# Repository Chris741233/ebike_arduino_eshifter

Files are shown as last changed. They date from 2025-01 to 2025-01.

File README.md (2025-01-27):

# ebike_arduino_eshifter
 eshifter for reconditioned VanMoof s5 ebike

Aide au membre de Cyclurba Kiki85 pour son reconditionnement d'un ebike VanMoof s5  
Aduino Nano/Uno, signal +5V, alim 9V.

**Discussion sur le forum Cyclurba**  - [Cyclurba](https://cyclurba.fr/forum/757849/programme-arduino-schifter.html?discussionID=31918)  
Site VanMoof - [VanMoof](https://www.vanmoof.com/fr-FR/our-rides/s5)

Librairies à installer, voir dossier "library_zip"  
Code de calibrage moteur et intensité, voir "arduino_eshifter_calibrage"  
Code d'utilisation voir "arduino_eshifter"  

---
#### VanMoof s5 eshifter
<p align="left">
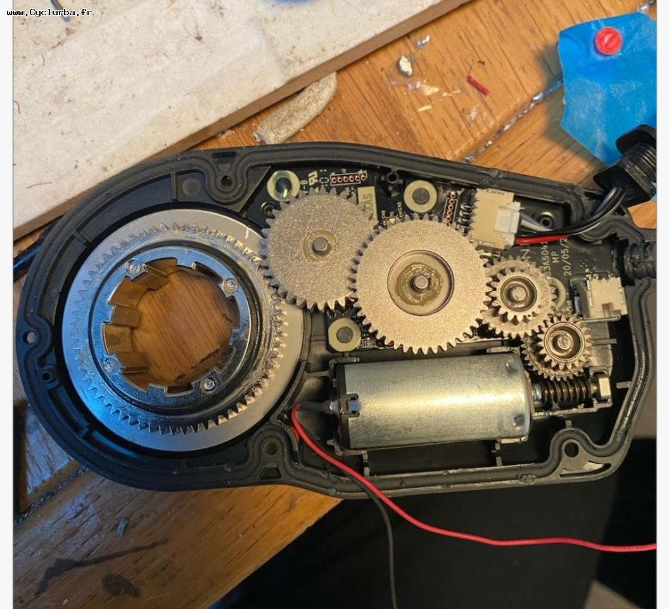
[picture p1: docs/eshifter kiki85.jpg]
  
</p>

#### Banc test : Arduino Uno/Nano + L298N + INA219
<p align="left">
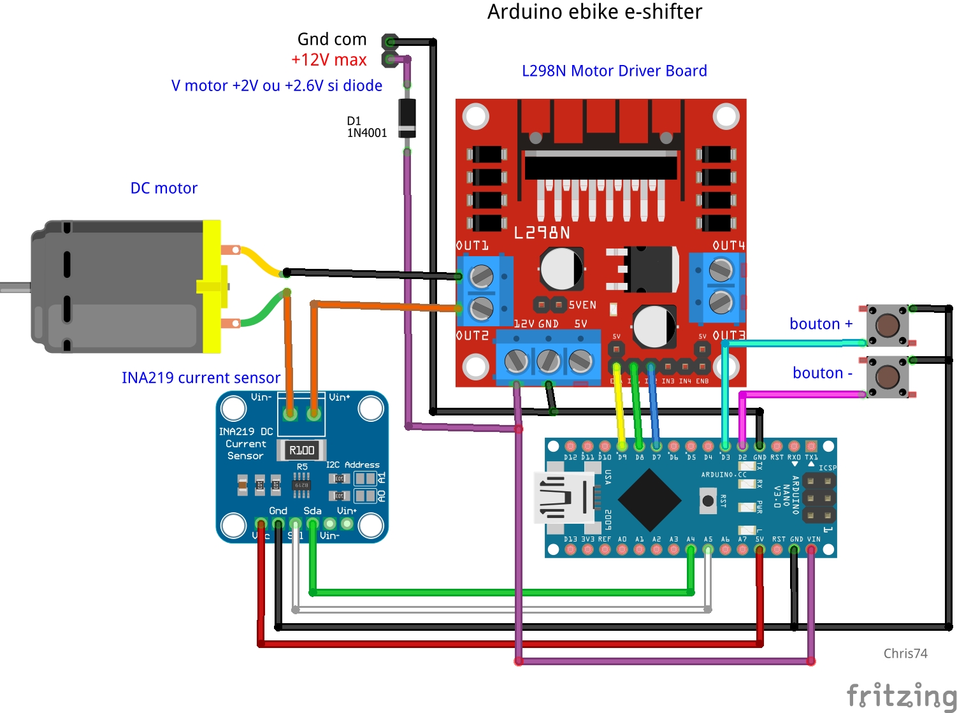
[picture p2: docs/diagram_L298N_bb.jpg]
  
</p>

#### Cavaliers circuit L298N
<p align="left">
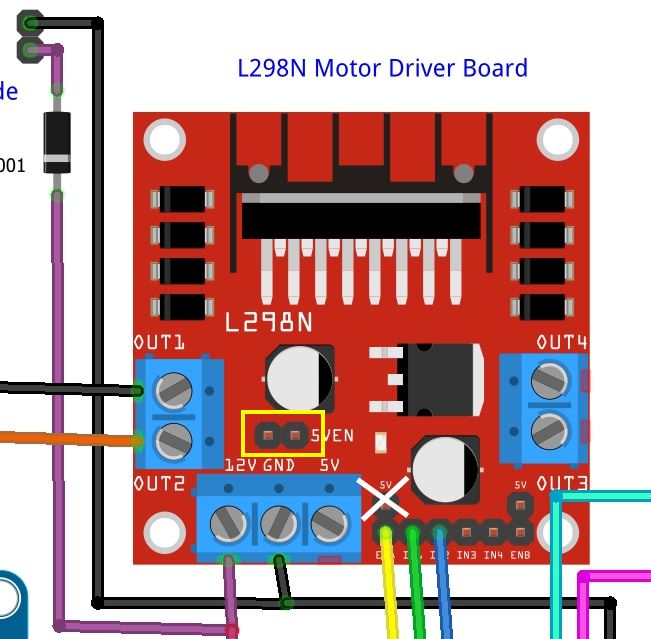
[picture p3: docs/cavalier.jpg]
  
</p>

#### Banc test
<p align="left">
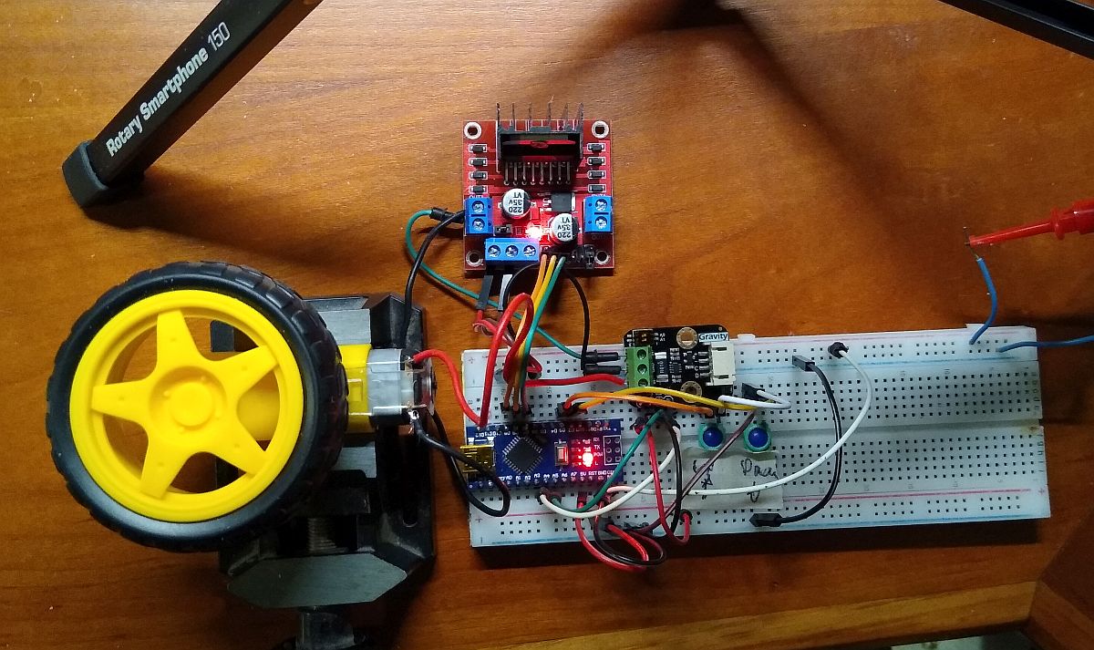
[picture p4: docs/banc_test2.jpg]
  
</p>

#### Console Serial (code de calibrage)
<p align="left">
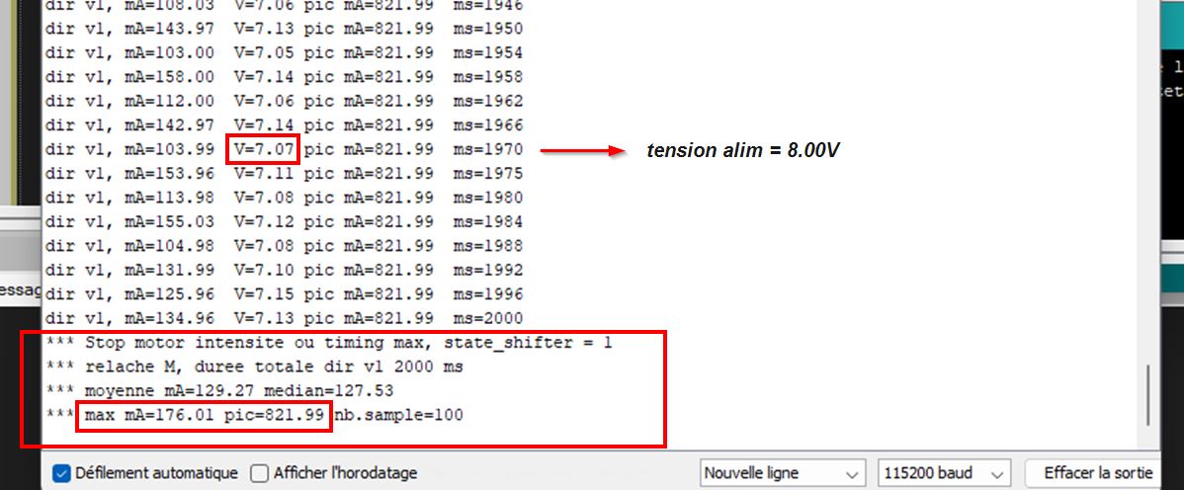
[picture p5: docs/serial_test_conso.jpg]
  
</p>
---

#### Utilisation
Régler les constantes en début de code selon vos essais, voir aussi le sujet sur le forum Cyclurba \
*Adjust constants at the beginning of code*

```
-- Setting ---

#define ADRESSE_INA 0x40     // adresse I2C INA219, generalement 0x40 (DFRobot=0x45) 
#define RSHUNT_INA 0.100     // valeur shunt, generalement R100 = 0.100 Ohm  (DFRobot=0.010) 
const int SPEED_MOTOR = 255; // speed moteur par defaut, 0 to 255 max (PWM 8bit)
const int MA_RUN = 360;      // (300) mA, conso en utilisation (sous ~6.5V au moteur)
const int MA_MARGE = 200;    // (150) mA, + marge de butee a pas depasser pour securite (stale = ? mA sous 8V)
const int MA_MAX = MA_RUN + MA_MARGE; 

// -- ces parametres influencent sur le controle intensite max moteur
const int SUP_PIC = 30;   // ms, filtrer les premieres ms du pic demarage moteur, env. 30-50=Ok ou 0 pour desactive
const int MIN_STAT = 20;  // mA, 20mA minimum pour etre affiche en direct et ajoute aux stats (laisser comme ca !)

const int TIMEOUT_1to3 = 2400;  // ms, temps de reference pour passer de v1 à v3 (butee basse a haute)
const int MARGE_HOME = 100;     // ms, petite marge a ajouter a TIMEOUT_1to3 pour etre sur de la position home v1 au boot
const int TIMEOUT_STEP = TIMEOUT_1to3/2; // ms, etape (1to2, 2to3, etc..), en principe TIMEOUT_1to3 / 2

const int DELAY_PUSH_BTN = 800; // ms, lorsqu'appui sur bouton et position atteinte (stop) = le delais d'attente avant reprise
// empeche relance moteur indesirable

const bool DOUBLE_CLIC_REINIT = true;  // reinit position home sur v1 si double-clic bouton down (descendre), true ou false

---
```

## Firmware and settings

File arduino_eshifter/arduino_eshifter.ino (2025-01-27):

/******************************************************************
Created with PROGRAMINO IDE for Arduino - 26.01.2025 | 13:38:17
Update      :
Author      : Chris74 pour Kiki85 (Cyclurba)
Description : e-shifter ebike Vanmoof s5, Arduino Nano

Github (codes et doc) : https://github.com/Chris741233/ebike_arduino_eshifter

forum Cyclurba : https://cyclurba.fr/forum/757849/programme-arduino-schifter.html?discussionID=31918


INA219 :
https://how2electronics.com/how-to-use-ina219-dc-current-sensor-module-with-arduino/
https://wiki.dfrobot.com/Gravity:%20I2C%20Digital%20Wattmeter%20SKU:%20SEN0291

L298N:
https://www.robotique.tech/tutoriel/commander-un-moteur-par-arduino-et-le-module-l298n/

conso montage a vide (Arduino nano + l298n + ina219) sous 8V = 29mA (sans USB, sans diode alim)

Voir aussi schema et script de calibration moteur et intensite

******************************************************************/


// -------- INCLUDE -------------------------------


#include <Wire.h>          // I2C
#include "INA219.h"        // from Rob.Tillaart, voir https://github.com/RobTillaart/INA219

// simplification envois Serial et screen serial, expl: Serial << "A:" << var << endl;
#include <Streaming.h>     // Peter Polidoro, https://github.com/janelia-arduino/Streaming    

// duree d'appui bouton et gestion bouton
// librairie du membre bricoleau, voir https://forum.arduino.cc/t/partage-boutons-poussoirs/361656
// pour info n'est pas dispo dans le depot officiel Arduino
#include "simpleBouton.h"  


#include <Timeout.h>       // timer, tfeldmann  https://github.com/tfeldmann/Arduino-Timeout 
// ne pas confondre avec TimeOut.h !


// -------- ARDUINO PIN, selon schema joint --------------

// butons
const int BUTON_UP_PIN = 3;    // bouton poussoir Plus (UP, Monter vers v3), interupt 3 possible  
const int BUTON_DOWN_PIN = 2;  // bouton poussoir Moins (DOWN, Descendre vers v1), interupt 2 possible

// L298N, motor driver
const int ENA_PIN = 9;   // enable A, PWM
const int IN1_PIN = 8;   // in1
const int IN2_PIN = 7;   // in2 

// LED interne Uno/Nano
const int LED_PIN = 13;  // LED_BUILTIN


// INA219 curent sensor  
// I2C PIN SDA A4, SCL A5


// --------  CONSTANTES SYSTEME, MODIFIABLES ------------------------


#define ADRESSE_INA 0x40     // adresse I2C INA219, generalement 0x40 (DFRobot=0x45) 
#define RSHUNT_INA 0.100     // valeur shunt, generalement R100 = 0.100 Ohm  (DFRobot=0.010) 

const int SPEED_MOTOR = 255; // speed moteur par defaut, 0 to 255 max (PWM 8bit)

const int MA_RUN = 360;      // (300) mA, conso en utilisation (sous ~6.5V au moteur)
const int MA_MARGE = 200;    // (150) mA, + marge de butee a pas depasser pour securite (stale = ? mA sous 8V)
const int MA_MAX = MA_RUN + MA_MARGE; 

// -- ces parametres influencent sur le controle intensite max moteur
const int SUP_PIC = 30;   // ms, filtrer les premieres ms du pic demarage moteur, env. 30-50ms=Ok ou 0 pour desactive
const int MIN_STAT = 20;  // mA, 20mA minimum pour etre affiche en direct et ajoute aux stats (laisser comme ca !)

const int TIMEOUT_1to3 = 2400;  // ms, temps de reference pour passer de v1 à v3 (butee basse a haute)
const int MARGE_HOME = 100;     // ms, petite marge a ajouter a TIMEOUT_1to3 pour etre sur de la position home v1 au boot
const int TIMEOUT_STEP = TIMEOUT_1to3/2; // ms, etape (1to2, 2to3, etc..), en principe TIMEOUT_1to3 / 2


const int DELAY_PUSH_BTN = 800; // ms, lorsqu'appui sur bouton et position atteinte (stop) = le delais d'attente avant reprise
// empeche relance moteur indesirable

const bool DOUBLE_CLIC_REINIT = false;  // reinit position home sur v1 si double-clic bouton down (descendre), true ou false



// -------- INIT OBJETS (ne pas modifier) ----------------------------

INA219 INA(ADRESSE_INA);   

simpleBouton boutonUp(BUTON_UP_PIN);      // objet bouton Plus  (UP, monter vers v3)
simpleBouton boutonDown(BUTON_DOWN_PIN);  // objet bouton Moins (DOWN, descendre vers v1)

boutonAction boutonD(BUTON_DOWN_PIN);


Timeout timer_motor; // objet timer pour gestion duree moteur


// --------  VARIABLES GLOBALES (ne pas modifier) ----------------------

// INA
float v_motor  = 0.0;
float mA_motor = 0.0;
float mW_motor = 0.0;
float shuntMv  = 0.0;
float pic_mA   = 0.0;  // stock val max


// etat position shifter
unsigned int state_shifter = 0;  // 0=inconnu, 1=V1, 2=V2, 3=V3

// etat moteur tourne, vrai/faux
bool motor_turn = false;

// etat bouton
bool state_btUp   = false; 
bool state_btDown = false;  
bool btpause      = false;  // pour limiter delais appui
bool blocage      = false;  // empeche appui 2 bt en meme temps

// -------- MAIN ----------------------



void setup()
{
    
    //pinMode(BUTON_UP_PIN, INPUT_PULLUP);    // appuyé = LOW, déja declare dans simpleBouton.h 
    //pinMode(BUTON_DOWN_PIN, INPUT_PULLUP);  // appuyé = LOW, déja declare dans simpleBouton.h 
    boutonD.attacher(simpleClicD, doubleClicD);
    
    
    // set all the motor control pins to outputs
    pinMode(ENA_PIN, OUTPUT);
    pinMode(IN1_PIN, OUTPUT);
    pinMode(IN2_PIN, OUTPUT);
    analogWrite(ENA_PIN, 0);  // PWM off
    
    // Led builtin Uno/Nano
    pinMode(LED_PIN, OUTPUT);
    digitalWrite(LED_PIN, LOW); 
    
    // stop moteur a l'initialisation
    stop_motor();   
    
    // Serial console
    Serial.begin(115200);
    
    Serial.println(__FILE__);
    Serial.print("INA219_LIB_VERSION: ");
    Serial.println(INA219_LIB_VERSION);
    
    Wire.begin();          // sda, scl
    Wire.setClock(400000); // fast I2C speed, a désactiver si pose problème
    if (!INA.begin() )
    {
        Serial.println("Could not connect INA219. Fix and Reboot");
    }
    
    // config shunt INA : "A max, R shunt"
    // INA.setMaxCurrentShunt(1, RSHUNT_INA);
    INA.setMaxCurrentShunt(2.5, RSHUNT_INA);     
    
    delay(100);
    
    // postionner moteur en vitesse 1, voir debut du Loop !
    
    
} // endsetup


void loop()
{
    v_motor  = INA.getBusVoltage();
    mA_motor = INA.getCurrent_mA();
    mW_motor = INA.getPower_mW();
    shuntMv  = INA.getShuntVoltage_mV();
    
    //Lecture de la durée d'appui boutons AVANT d'actualiser
    //uint32_t dureeUp   = boutonUp.dureeEnfonce();  
    //uint32_t dureeDown = boutonDown.dureeEnfonce(); 
    boutonUp.actualiser();
    boutonDown.actualiser();
    boutonD.actualiser();     // pour double clic bt.down ! (cf function)
    
    unsigned int mstartmotor; // pour temps a deduire au start motor (cont. intensite)
    if(state_shifter==0) mstartmotor = (TIMEOUT_1to3+MARGE_HOME)-SUP_PIC;
    if(state_shifter>0) mstartmotor = TIMEOUT_STEP-SUP_PIC;
    
    //Gestion du petit malin qui appuie sur les deux boutons en même temps
    if (boutonUp.estEnfonce() && boutonDown.estEnfonce()) blocage = true;
    if (boutonUp.estRelache() && boutonDown.estRelache()) blocage = false;
    if (blocage) return;
    
    
    // Au boot, si aucune position definie (0), on descend a la butee basse sur v1 
    if(state_shifter < 1 && !motor_turn) {
        
        Serial << "to Home v1" << endl;
        timer_motor.start(TIMEOUT_1to3 + MARGE_HOME );  // trajet au plus long + petite marge
        turn_motor_down();   // move motor DOWN
        state_btDown = true; // simuler etat bouton 
    }
    else {
        
        // -- Bouton UP, MONTER vers v3 --
        if (boutonUp.vientDEtreEnfonce() && !motor_turn && state_shifter < 3) {
            Serial << "appui bt UP" << endl;
            state_btUp = true;
            timer_motor.start(TIMEOUT_STEP);
            turn_motor_up(); // move motor UP
            
            state_shifter+=1;
            
            // pas d'instruction delay() ici !!
        }
        
        // -- Bouton DOWN, DESCENDRE vers v1 --
        if (boutonDown.vientDEtreEnfonce() && !motor_turn && state_shifter > 1) {
            Serial << "appui bt DOWN" << endl;
            state_btDown = true;
            timer_motor.start(TIMEOUT_STEP);
            turn_motor_down(); // move motor DOWN
            
            state_shifter-=1;
            
            // pas d'instruction delay() ici !!
        }
    } // endelse
    
    
    if(!timer_motor.time_over() && timer_motor.time_left_ms() % 100 == 0) {
        Serial << timer_motor.time_left_ms() << endl; // debug, decompte timer tous les 100
    }
    
    // controle depassement intensite (en deduisant demarage moteur)
    if (timer_motor.time_left_ms() < mstartmotor && abs(mA_motor) >= MA_MAX) {
        stop_motor();
        timer_motor.expire();  // timer off
        if(state_shifter<1) state_shifter=1; // init sur v1 apres le home
        
        Serial << "STOP mA! mA=" << mA_motor << " state v=" << state_shifter << endl;
        if(state_btUp || state_btDown) {
            btpause      = true;
            state_btUp   = false;
            state_btDown = false;
        }
        // pas d'instruction delay() ici !!
    } // endif timer
    
    // timer termine
    if(timer_motor.time_over()) {
        stop_motor(); 
        if(state_shifter<1) state_shifter=1; // init sur v1 apres le home
        
        //Serial << "STOP timer, state v=" << state_shifter << endl; // debug
        if(state_btUp || state_btDown) {
            btpause      = true;
            state_btUp   = false;
            state_btDown = false;
        }
        // pas d'instruction delay() ici !!
    } // endif timer
    
    // -- pause reprise boutons
    if(btpause) {
        Serial << "pause reprise (" << DELAY_PUSH_BTN << " ms) state_shifter=v" << state_shifter << endl; 
        delay(DELAY_PUSH_BTN); 
        btpause = false; 
    }
    
} // endloop



// ------------- FUNCTIONS ---------------------------


// double-clic bouton down : reinit position home (down to v1) 
void doubleClicD() {
    if(DOUBLE_CLIC_REINIT) {
        // RAZ
        state_btUp    = false; 
        state_btDown  = false;  
        state_shifter = 0;  
        Serial.println("double clic bt down : REINIT HOME v1!"); 
    }
} // endfunc

void simpleClicD() { 
    //Serial.println("simple clic bt down"); // pas utilise
    //
} // endfunc


// stop motor
void stop_motor() {
    digitalWrite(IN1_PIN, LOW);
    digitalWrite(IN2_PIN, LOW);
    analogWrite(ENA_PIN, 0);  // PWM off 
    motor_turn = false;
    digitalWrite(LED_PIN, LOW); // led nano
} //endfunc

// marche avant (PLUS, UP, MONTER)
bool turn_motor_up() {
    digitalWrite(IN1_PIN, HIGH);
    digitalWrite(IN2_PIN, LOW);
    analogWrite(ENA_PIN, SPEED_MOTOR);  // choix PWM
    motor_turn = true;
    digitalWrite(LED_PIN, HIGH); // led nano
} //endfunc


// marche arriere (MOINS, DOWN, DESCENDRE)
bool turn_motor_down() {
    digitalWrite(IN1_PIN, LOW);
    digitalWrite(IN2_PIN, HIGH);
    analogWrite(ENA_PIN, SPEED_MOTOR);  // choix PWM
    motor_turn = true;
    digitalWrite(LED_PIN, HIGH); // led nano
} //endfunc
